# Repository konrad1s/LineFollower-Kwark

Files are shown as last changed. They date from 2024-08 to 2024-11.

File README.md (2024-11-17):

## Introduction

The LineFollower Robot is an autonomous robot designed to follow a predefined path marked by a black or white line.<br>
This project serves a quite advanced solution including hardware project, embedded software and PC QT application.

A short video demo is available on [YouTube](https://www.youtube.com/watch?v=Kh0NfI-lTgY).

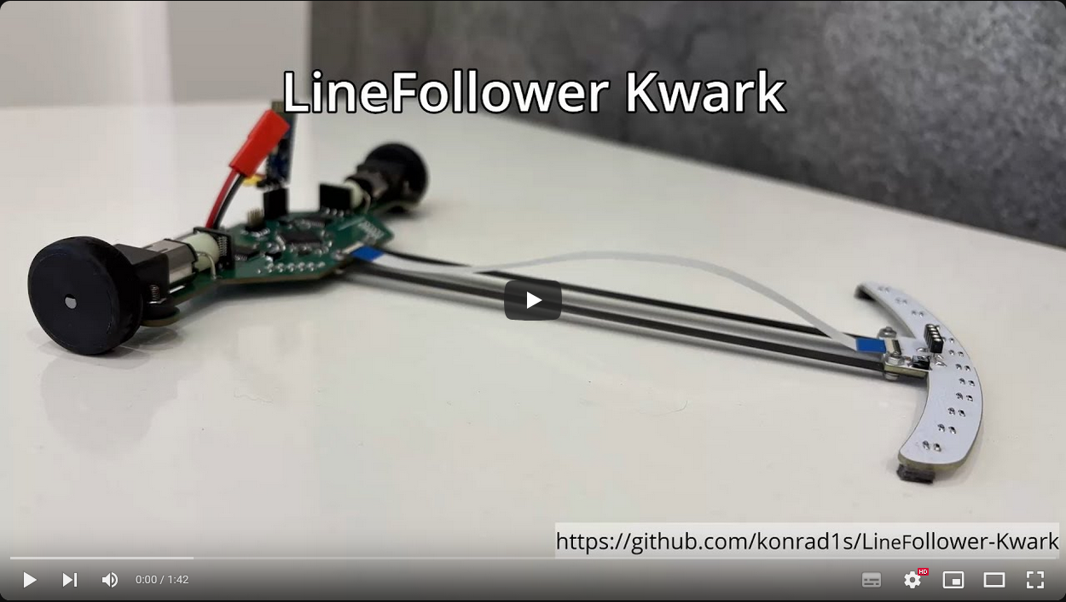
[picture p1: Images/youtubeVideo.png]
LineFollower Youtube Video (https://www.youtube.com/watch?v=Kh0NfI-lTgY)


Example - one of the first - linefollower run:
<p align="center">
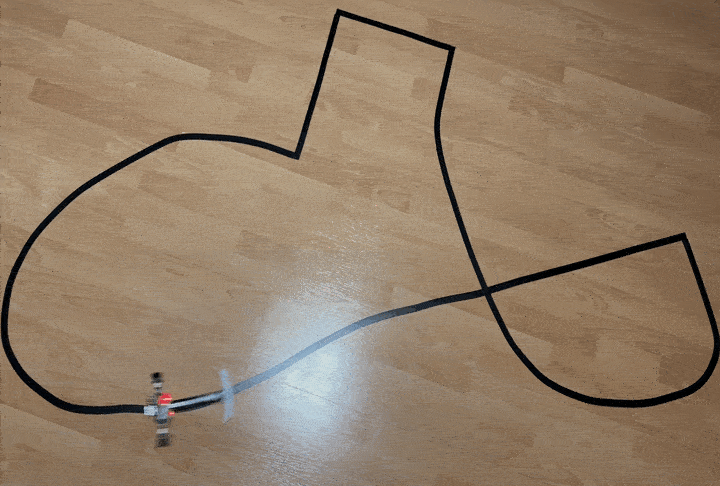
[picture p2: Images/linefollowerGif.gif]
  
</p>

## Hardware
### **High level block diagram**

[![](https://mermaid.ink/img/pako:eNqVlW1vmzAQx7-K5ddJGiCEBE2T8tB2VWHJIM2kOVXlBjdBAxw59tb04bvPxk0ChLYaL8Bnfvf33dkcz3BJIwJduGJ4swaz4SJbZEBeW3Gvp0Y0TUUWLzGPaQZQybzVrLqGiSCc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)](https://mermaid.live/edit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)

### **Schematic and PCB**
Electronic circuit diagrams are available in the [Hardware/release/schematic](Hardware/release/schematic) folder.<br>
Gerbers files are available in the [Hardware/release/gerbers](Hardware/release/gerbers) folder.

**Main board:**
<p align="center">
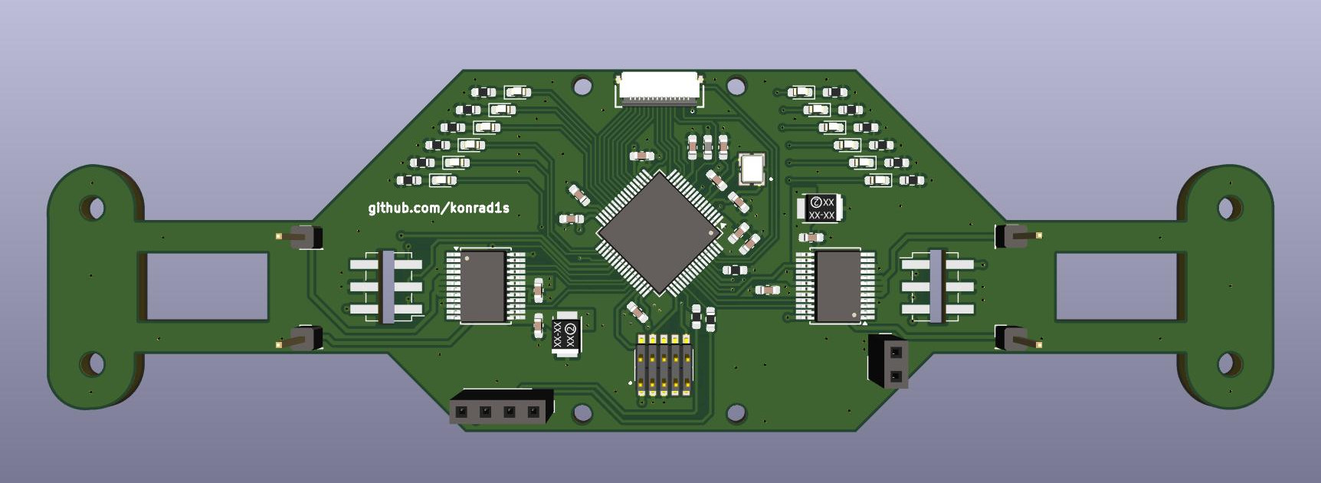
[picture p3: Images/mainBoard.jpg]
  
</p>

**Sensor board:**
<p align="center">
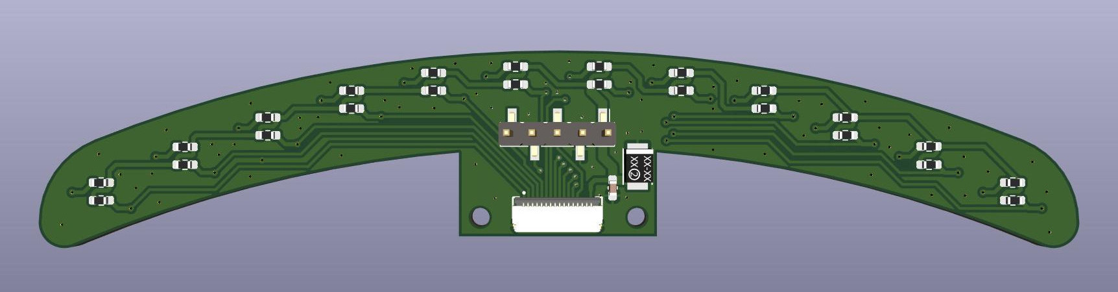
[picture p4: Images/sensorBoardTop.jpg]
  
</p>

**Encoder board:**
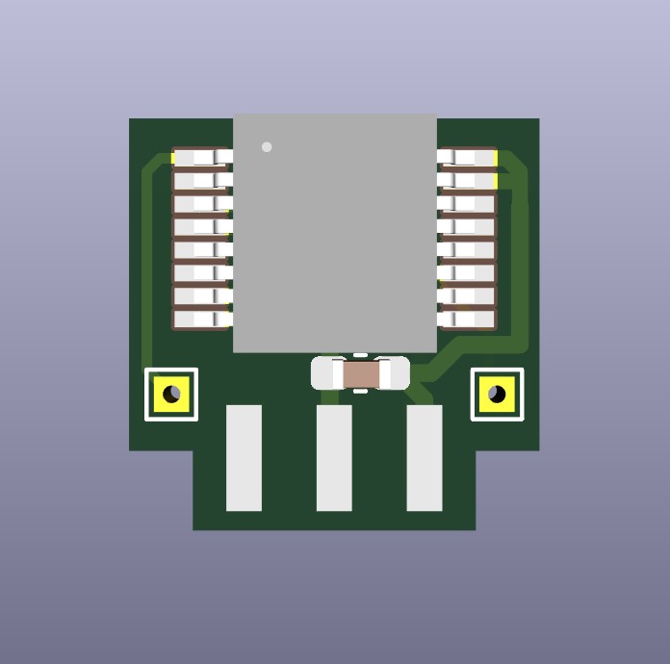
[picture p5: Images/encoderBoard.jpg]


### **Component Details**
1. **STM32F722 MCU** <br>
ARM Cortex M7 microcontroller operating at the 216MHz with FPU, Cache, ITCM, DTCM. It powerful enough to handle algorithms and real-time processing required in linefollower applications.
3. **12x KTIR0711S** <br>
Phototransistor-based infrared sensors used to detect the line by measuring reflected IR light. Arranged in a array at the front of the robot to detect the position of the line. Outputs are connected to the MCU's ADC channels for monitoring.
4. **12x LEDs** <br>
Each LED corresponds to a KTIR0711S sensor, turned on when the sensor detects the line.
5. **2x AMS AS5040 Encoders** <br>
10-bit contactless magnetic rotary encoders providing precise angular position measurements. Thanks to the closed-loop control, encoders enables precise control of motor by providing feedback (velocity) for PID controllers.
6. **2x Pololu TB6612FNG Motor Driver Modules** <br>
H-bridge motor driver modules capable of controlling DC motors. Controller channels are combined to obtain higher current capacity.
7. **2x Pololu Motor 10:1 HPCB 6V DC Motors** <br>
High-power micro metal gearmotors with a 10:1 gear ratio
8. **Bluetooth Module JDY-31** <br>
Bluetooth serial module enables wireless communication between the robot and PC application.
9. **Power Supply Components** <br>
LiPo 7.4V battery used due to high energy density and ability to deliver powerful burst of current.<br>
3.3V Low dropout voltage regulator - steps down the battery voltage for MCU, sensors and others modules.

## Software

### **Main run loop**

The core functionality is implemented through an event-driven state machine. The primary signal is the LF_SIG_ADC_DATA_UPDATED, which is raised whenever new ADC data is available. Currently every 5ms, however increasing this frequency can lead to better control results.

The activity diagram presents simplified main robot algorithm in RUN state:
<p align="center">
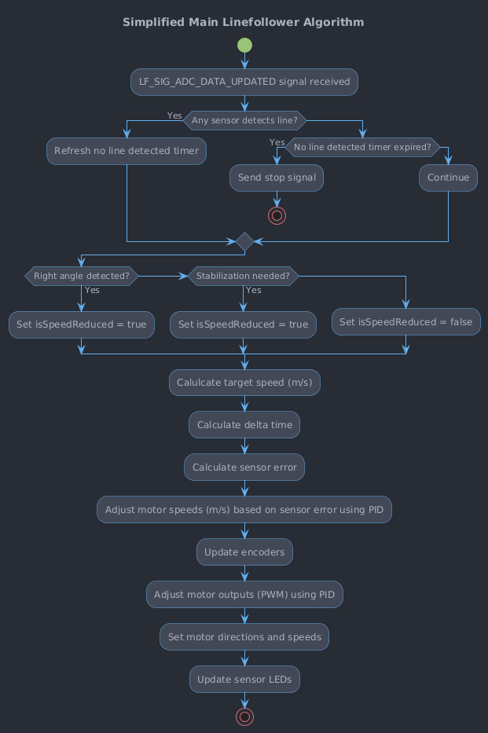
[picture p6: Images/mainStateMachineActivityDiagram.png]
  
</p>

### **Code Structure**

Short brief about implemented software components:

- **linefollower:**
The core component of the software, manages the main event driven state machine. It handles the initialization of all subsystems. This component integrates sensor data processing, PID control algorithms, encoder feedback, and motor management. Additionally, it facilitates communication with the PC application for debugging and configuration purposes.
- **linefollower_config:**
Defines the default configurations and settings for the robot. This ensures that all hardware related configurations is easily adjustable.
- **lf_signal_queue:**
Implements a signal queue used for managing events and signals within the state machine.
- **linefollower_commands:**
Handles the processing of serial communication protocol (SCP) commands received from the PC application. It defines a set of commands for controlling the robot's modes, resetting the MCU, initiating calibration, reading and writing NVM data, toggling debug mode, retrieving session information, and entering the bootloader for firmware updates.
- **lf_calibrate:**
Manages the calibration process for the sensors. It handles the collection of sensor data during calibration runs, computes appropriate threshold values based on the collected values.
- **sensors:**
The module is responsible for interfacing with the robot's sensors to detect the line. It processes ADC data to determine states and manages the associated LEDs. Also implements algorithms to detect specific straight lines and right angles.
- **pid:**
Implements the PID control algorithms used to regulate the robot's motor speeds based on sensor and encoder feedback.
- **encoder:**
Manages the interfacing with the motor encoders to track the robot's velocity.
- **tb6612_motor:**
The module interfaces with the TB6612 motor driver hardware to control the robot's motors.
- **nvm:**
The module handles non-volatile memory operations, enabling the storage and retrieval of configuration data, calibration settings, and runtime parameters. The module ensures data integrity through CRC verification. The nvm module allows the robot to retain configurations across power cycles.
- **scp:**
Implements the Serial Communication Protocol (SCP) used for communication between the robot and external interfaces such as the PC application.
- **scp_dispatcher:**
The module acts as a handler for processing SCP commands received via the scp module. It manages a global command queue using a circular buffer to store incoming data, parses SCP packets, verifies data integrity using CRC, and dispatches valid commands to their respective handlers.

## Bootloader
Implemented bootloader allows for over the air firmware updates without the need of programmer. This is particularly useful for making quick updates "on the road." The bootloader uses the implemented SCP (Serial Communication Protocol) to receive firmware updates over Bluetooth.

There are 2 methods to enter the Bootloader:
1. **Command-Based Entry From Application** <br>
Send a specific command to trigger reset to the bootloader.
2. **Backdoor Entry** <br>
Enter the bootloader upon power-up by sending a specific command. Ensures that firmware updates are always possible, even if the application has errors causing continuous resets.

FLASH memory layout:
<p align="center">
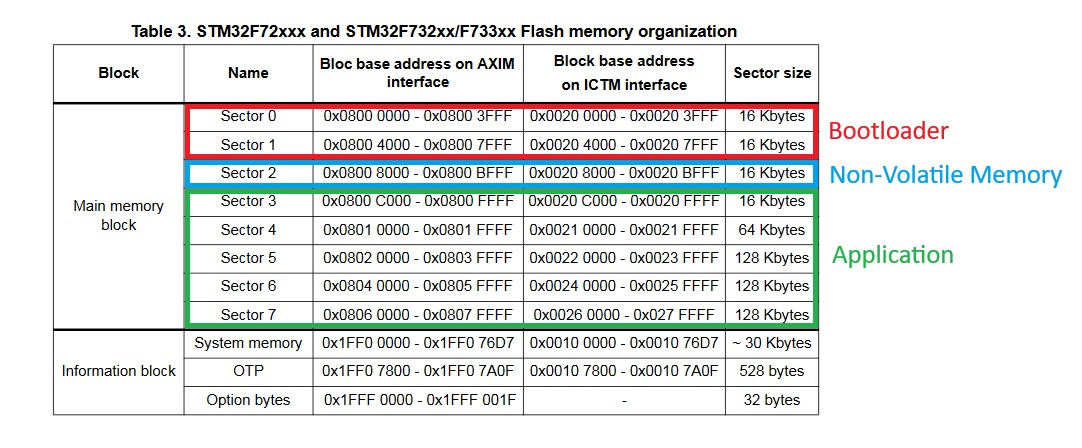
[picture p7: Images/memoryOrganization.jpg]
  
</p>

## **QT Application**

The QT Application provides a graphical interface to control, configure, and monitor the robot. The main sections of the interface and their functionalities are as follows:
1. **Connection Panel** <br>
Connection indicator and buttons to establish or terminate Bluetooth communication.
2. **Control Panel**<br>
Starting, stopping, resetting, and calibrating the robot, along with options to enable debug mode, read/write NVM, and display real-time data (speed, error, and timing metrics).
3. **Sensors Panel**<br>
Real-time sensor data display showing actual values, calibration references, and sensor weights.
4. **Configuration**<br>
Includes settings for general parameters, PID tuning for motor control, and encoder adjustments.
5. **Graph**<br>
A real-time graph displaying motor speeds, speed reduction, sensors error, enabling data analysis and adjustments for optimal performance.
6. **Bootloader**<br>
Firmware update controls, including options to enter bootloader mode, switch to the main application and flash new firmware via Bluetooth.
7. **Logs**<br>
Real-time log display with options to save or clear logs, providing detailed event tracking for debugging.

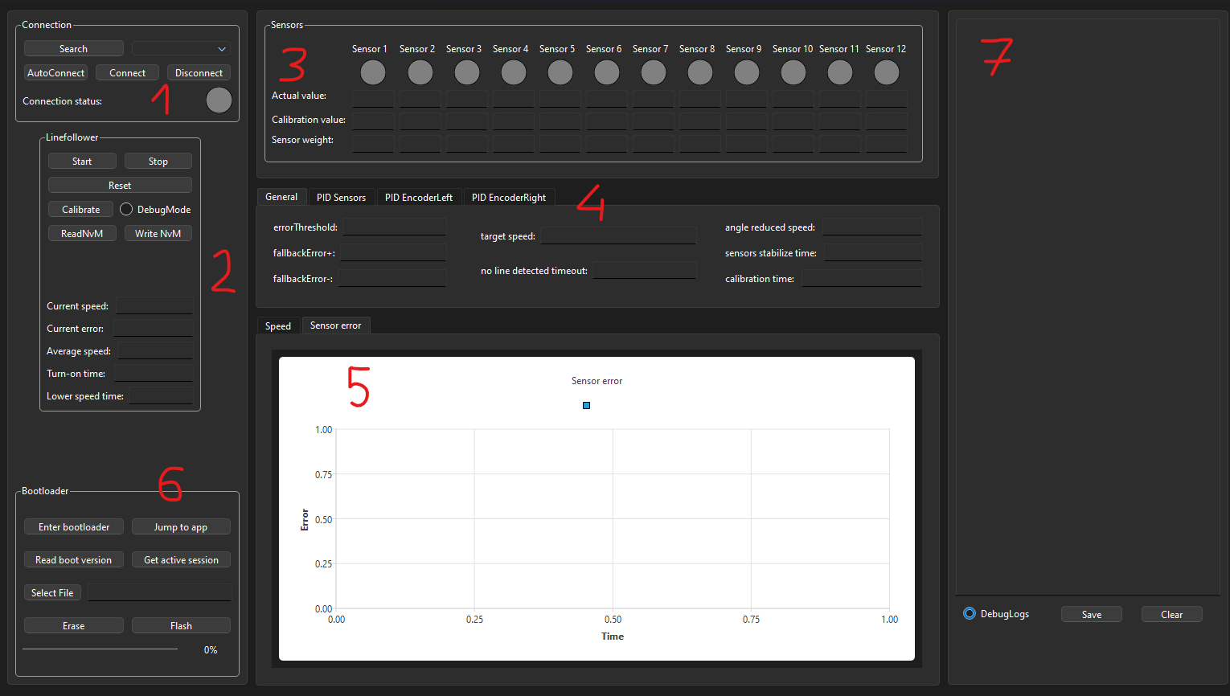
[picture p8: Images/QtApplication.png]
QtApplication


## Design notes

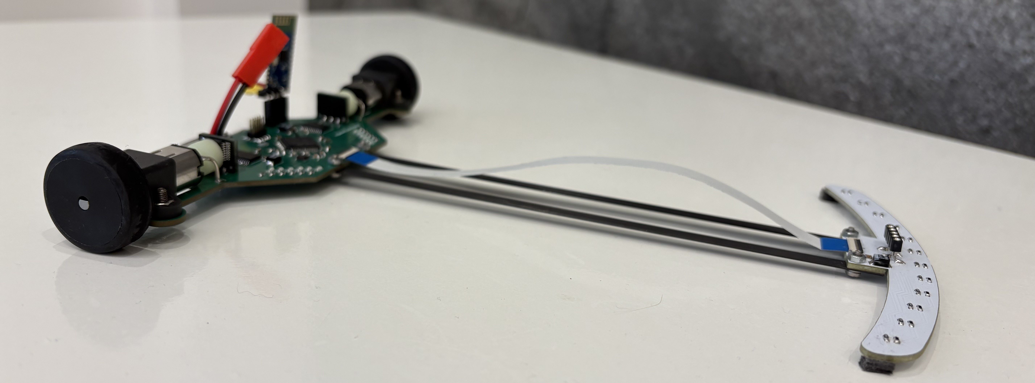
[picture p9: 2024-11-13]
Images/linefollower.jpg

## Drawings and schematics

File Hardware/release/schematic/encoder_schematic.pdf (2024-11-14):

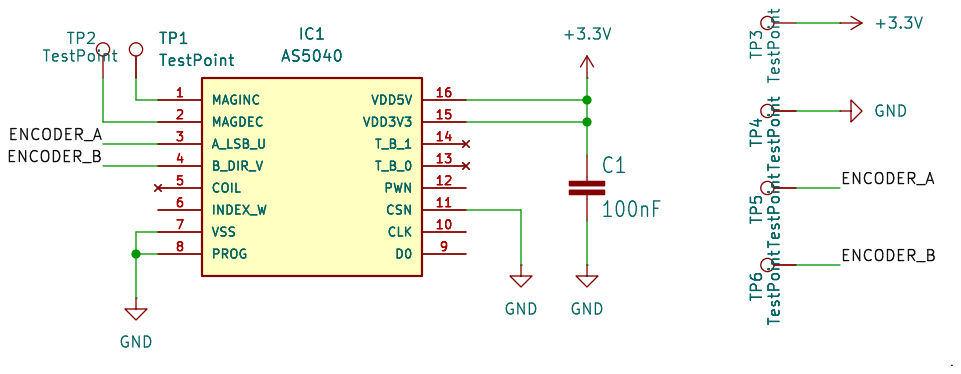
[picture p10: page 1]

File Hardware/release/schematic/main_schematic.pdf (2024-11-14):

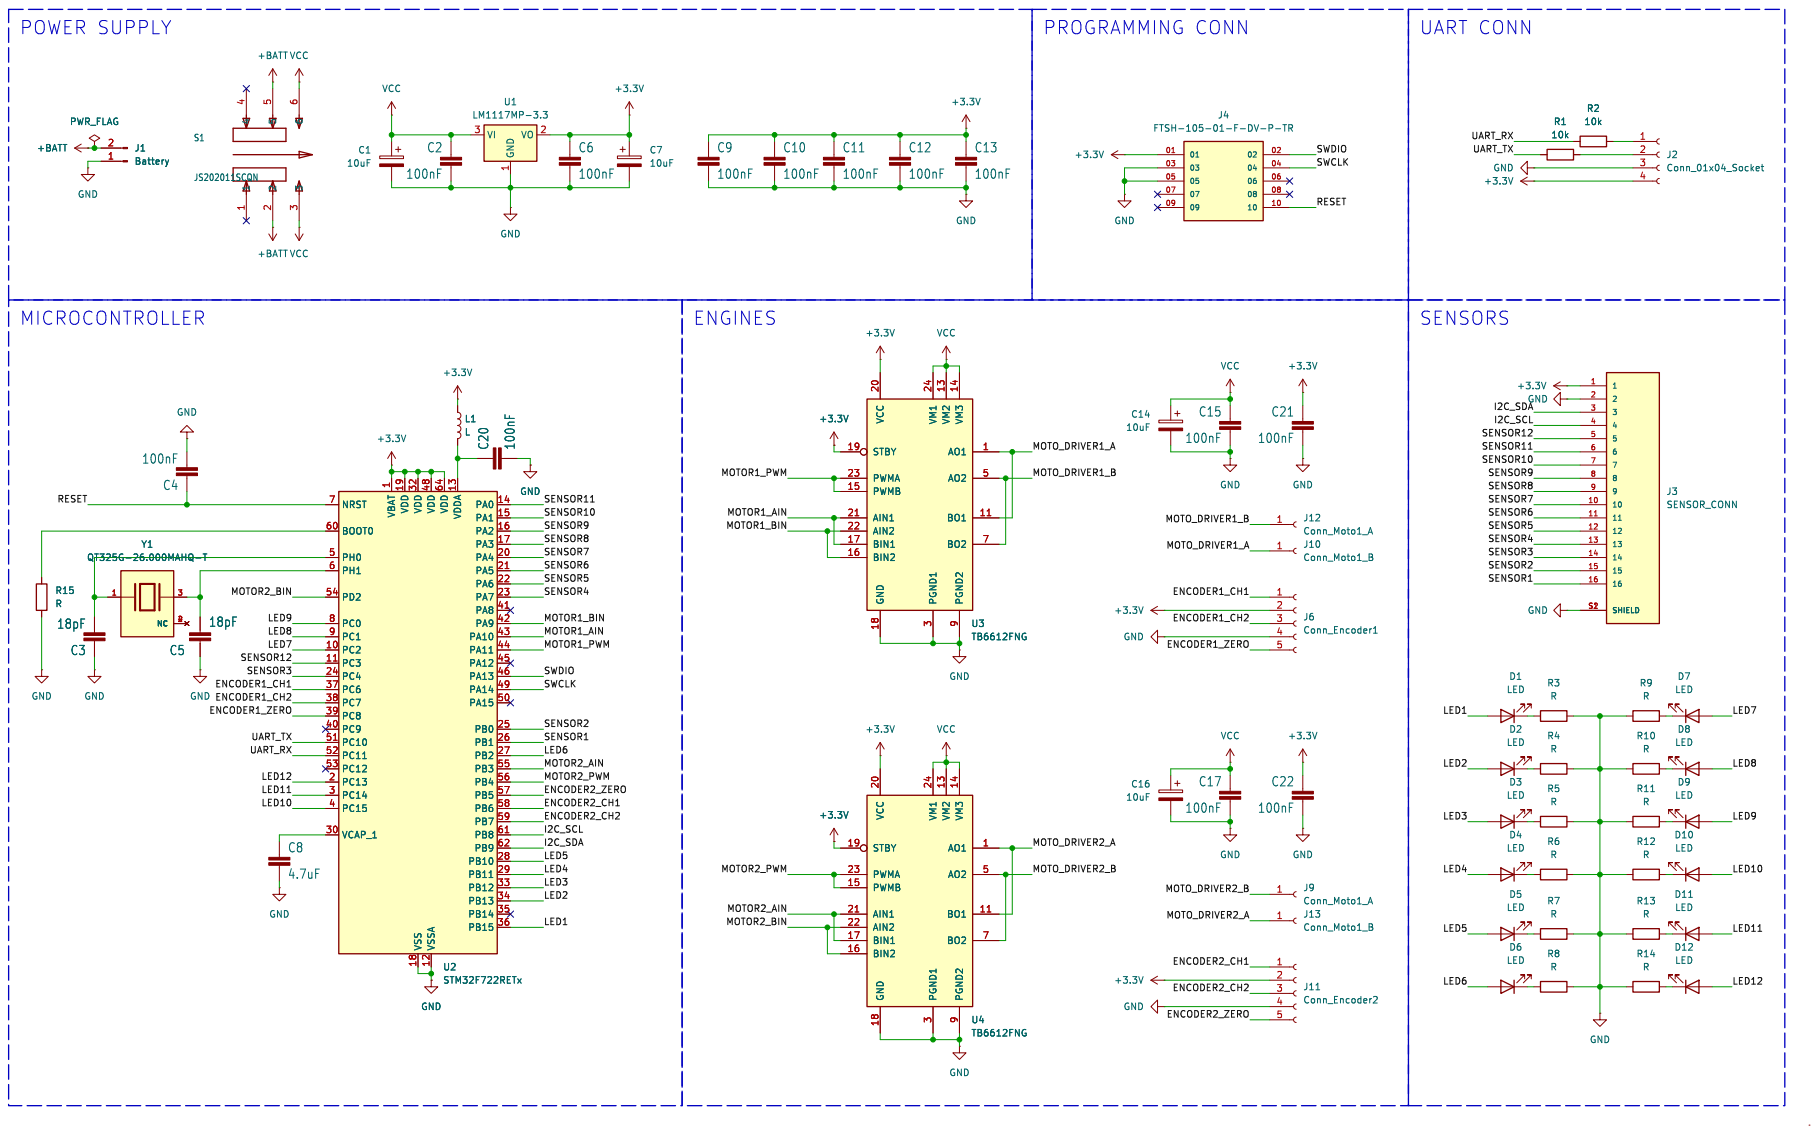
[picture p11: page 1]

1 PC2 10 PC3 11 VSSA 12 VDDA 13 PA0 14 PA1 15 PA2 16 PA3 17 VSS 18 VDD 19 PC13 2 PA4 20 PA5 21 PA6 22 PA7 23 PC4 24 PB0 25 PB1 26 PB2 27 PB10 28 PB11 29 PC14 3 VCAP_1 30 VDD 32 PB12 33 PB13 34 PB14 35 PB15 36 PC6 37 PC7 38 PC8 39 PC15 4 PC9 40 PA8 41 PA9 42 PA10 43 PA11 44 PA12 45 PA13 46 VDD 48 PA14 49 PH0 5 PA15 50 PC10 51 PC11 52 PC12 53 PD2 54 PB3 55 PB4 56 PB5 57 PB6 58 PB7 59 PH1 6 BOOT0 60 PB8 61 PB9 62 VDD 64 NRST 7 PC0 8 PC1 9 GND C3

1 PC2 10 PC3 11 VSSA 12 VDDA 13 PA0 14 PA1 15 PA2 16 PA3 17 VSS 18 VDD 19 PC13 2 PA4 20 PA5 21 PA6 22 PA7 23 PC4 24 PB0 25 PB1 26 PB2 27 PB10 28 PB11 29 PC14 3 VCAP_1 30 VDD 32 PB12 33 PB13 34 PB14 35 PB15 36 PC6 37 PC7 38 PC8 39 PC15 4 PC9 40 PA8 41 PA9 42 PA10 43 PA11 44 PA12 45 PA13 46 VDD 48 PA14 49 PH0 5 PA15 50 PC10 51 PC11 52 PC12 53 PD2 54 PB3 55 PB4 56 PB5 57 PB6 58 PB7 59 PH1 6 BOOT0 60 PB8 61 PB9 62 VDD 64 NRST 7 PC0 8 PC1 9 U2STM32F722RETx C8

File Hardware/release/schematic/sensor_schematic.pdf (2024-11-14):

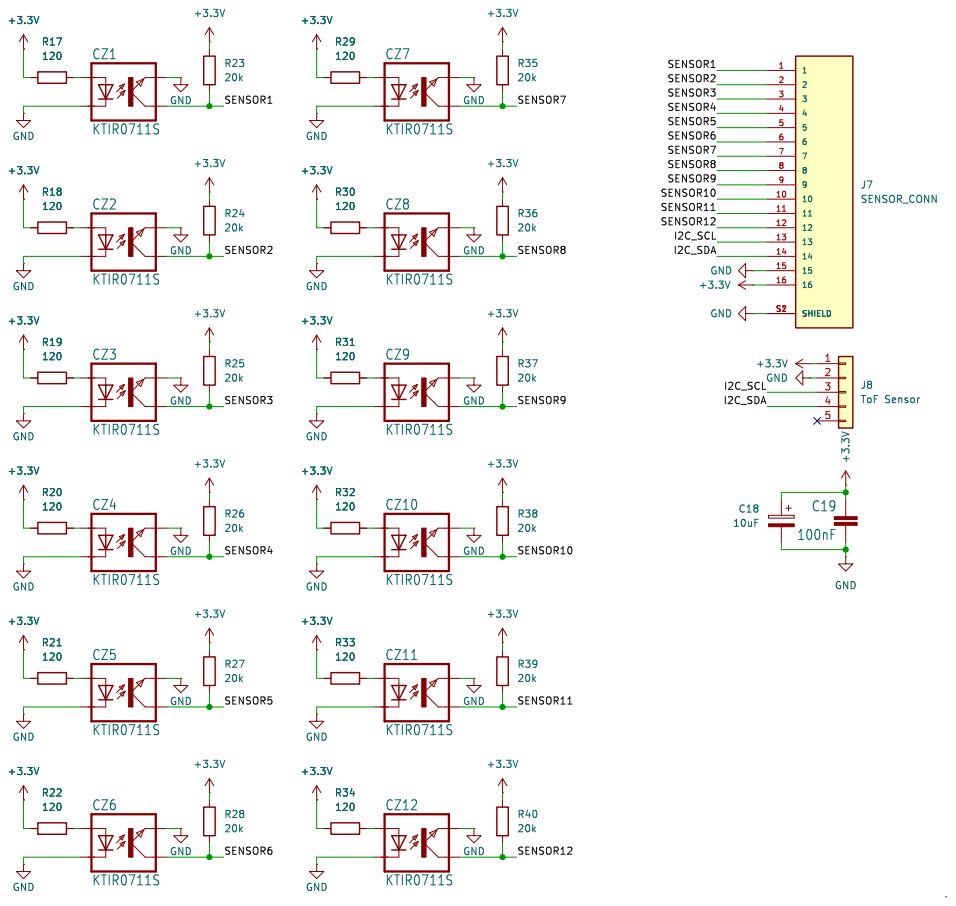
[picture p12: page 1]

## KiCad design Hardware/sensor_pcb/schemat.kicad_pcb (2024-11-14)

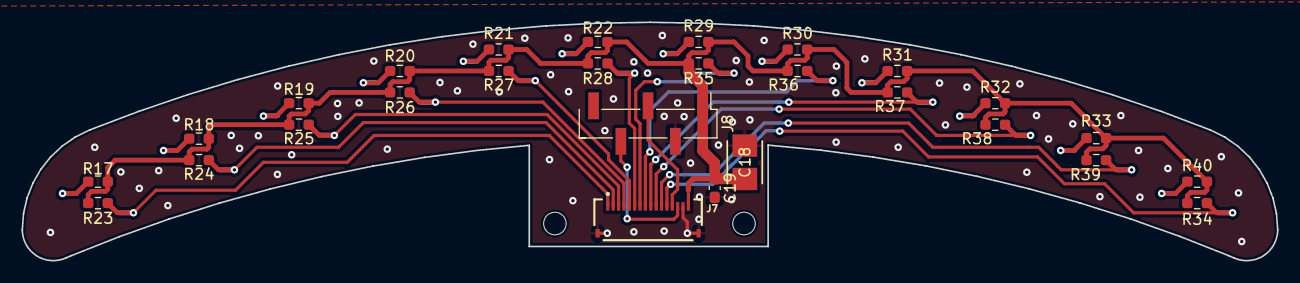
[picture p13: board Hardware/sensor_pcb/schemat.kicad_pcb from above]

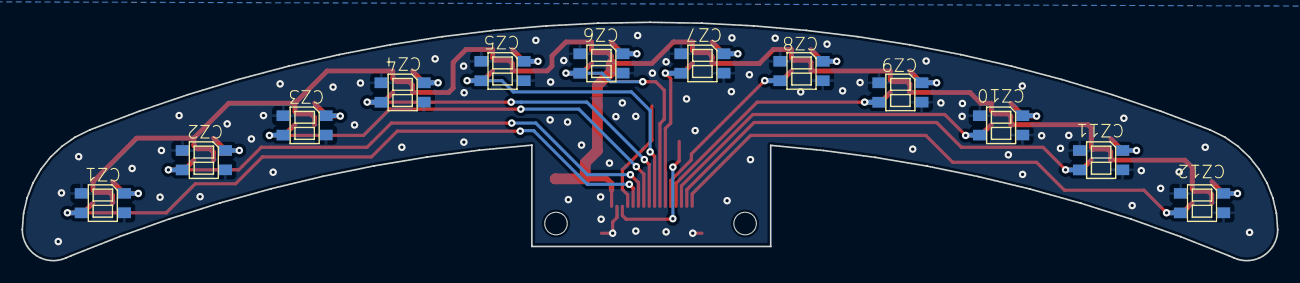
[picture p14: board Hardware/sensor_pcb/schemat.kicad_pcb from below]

Board: 2 copper layers, 116.8 x 22.2 mm, 42 parts (12 on the bottom side), 28 nets.

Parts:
@HOLE8, @HOLE9: (no value)
C18: 10uF; CAP_293D-B_VSS
C19: 100nF; C_0603_1608Metric_Pad1.08x0.95mm_HandSolder
CZ1, CZ2, CZ3, CZ4, CZ5, CZ6, CZ7, CZ8, CZ9, CZ10, CZ11, CZ12: KTIR0711S; TOP
J7: SENSOR_CONN; GCT_FFC2B28-16-G
J8: ToF Sensor; PinHeader_1x05_P2.54mm_Vertical_SMD_Pin1Left
R17, R18, R19, R20, R21, R22, R29, R30, R31, R32, R33, R34: 120; R_0603_1608Metric_Pad0.98x0.95mm_HandSolder
R23, R24, R25, R26, R27, R28, R35, R36, R37, R38, R39, R40: 20k; R_0603_1608Metric_Pad0.98x0.95mm_HandSolder

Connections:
+3.3V: C18.1, C19.1, J7.16, J8.1, R17.1, R18.1, R19.1, R20.1, R21.1, R22.1, R23.1, R24.1, R25.1, R26.1, R27.1, R28.1, R29.1, R30.1, R31.1, R32.1, R33.1, R34.1, R35.1, R36.1, R37.1, R38.1, R39.1, R40.1
/schemat_2/I2C_SCL: J7.13, J8.3
/schemat_2/I2C_SDA: J7.14, J8.4
/schemat_2/SENSOR1: CZ12.KOLEKTOR, J7.1, R23.2
/schemat_2/SENSOR2: CZ11.KOLEKTOR, J7.2, R24.2
/schemat_2/SENSOR3: CZ10.KOLEKTOR, J7.3, R25.2
/schemat_2/SENSOR4: CZ9.KOLEKTOR, J7.4, R26.2
/schemat_2/SENSOR5: CZ8.KOLEKTOR, J7.5, R27.2
/schemat_2/SENSOR6: CZ7.KOLEKTOR, J7.6, R28.2
/schemat_2/SENSOR7: CZ6.KOLEKTOR, J7.7, R35.2
/schemat_2/SENSOR8: CZ5.KOLEKTOR, J7.8, R36.2
/schemat_2/SENSOR9: CZ4.KOLEKTOR, J7.9, R37.2
/schemat_2/SENSOR10: CZ3.KOLEKTOR, J7.10, R38.2
/schemat_2/SENSOR11: CZ2.KOLEKTOR, J7.11, R39.2
/schemat_2/SENSOR12: CZ1.KOLEKTOR, J7.12, R40.2
GND: C18.2, C19.2, CZ1.EMITER, CZ1.KATODA, CZ2.EMITER, CZ2.KATODA, CZ3.EMITER, CZ3.KATODA, CZ4.EMITER, CZ4.KATODA, CZ5.EMITER, CZ5.KATODA, CZ6.EMITER, CZ6.KATODA, CZ7.EMITER, CZ7.KATODA, CZ8.EMITER, CZ8.KATODA, CZ9.EMITER, CZ9.KATODA, CZ10.EMITER, CZ10.KATODA, CZ11.EMITER, CZ11.KATODA, CZ12.EMITER, CZ12.KATODA, J7.15, J7.S1 (SHIELD), J7.S2 (SHIELD), J8.2
unnamed: CZ1.ANODA, R34.2
unnamed: CZ2.ANODA, R33.2
unnamed: CZ3.ANODA, R32.2
unnamed: CZ4.ANODA, R31.2
unnamed: CZ5.ANODA, R30.2
unnamed: CZ6.ANODA, R29.2
unnamed: CZ7.ANODA, R22.2
unnamed: CZ8.ANODA, R21.2
unnamed: CZ9.ANODA, R20.2
unnamed: CZ10.ANODA, R19.2
unnamed: CZ11.ANODA, R18.2
unnamed: CZ12.ANODA, R17.2

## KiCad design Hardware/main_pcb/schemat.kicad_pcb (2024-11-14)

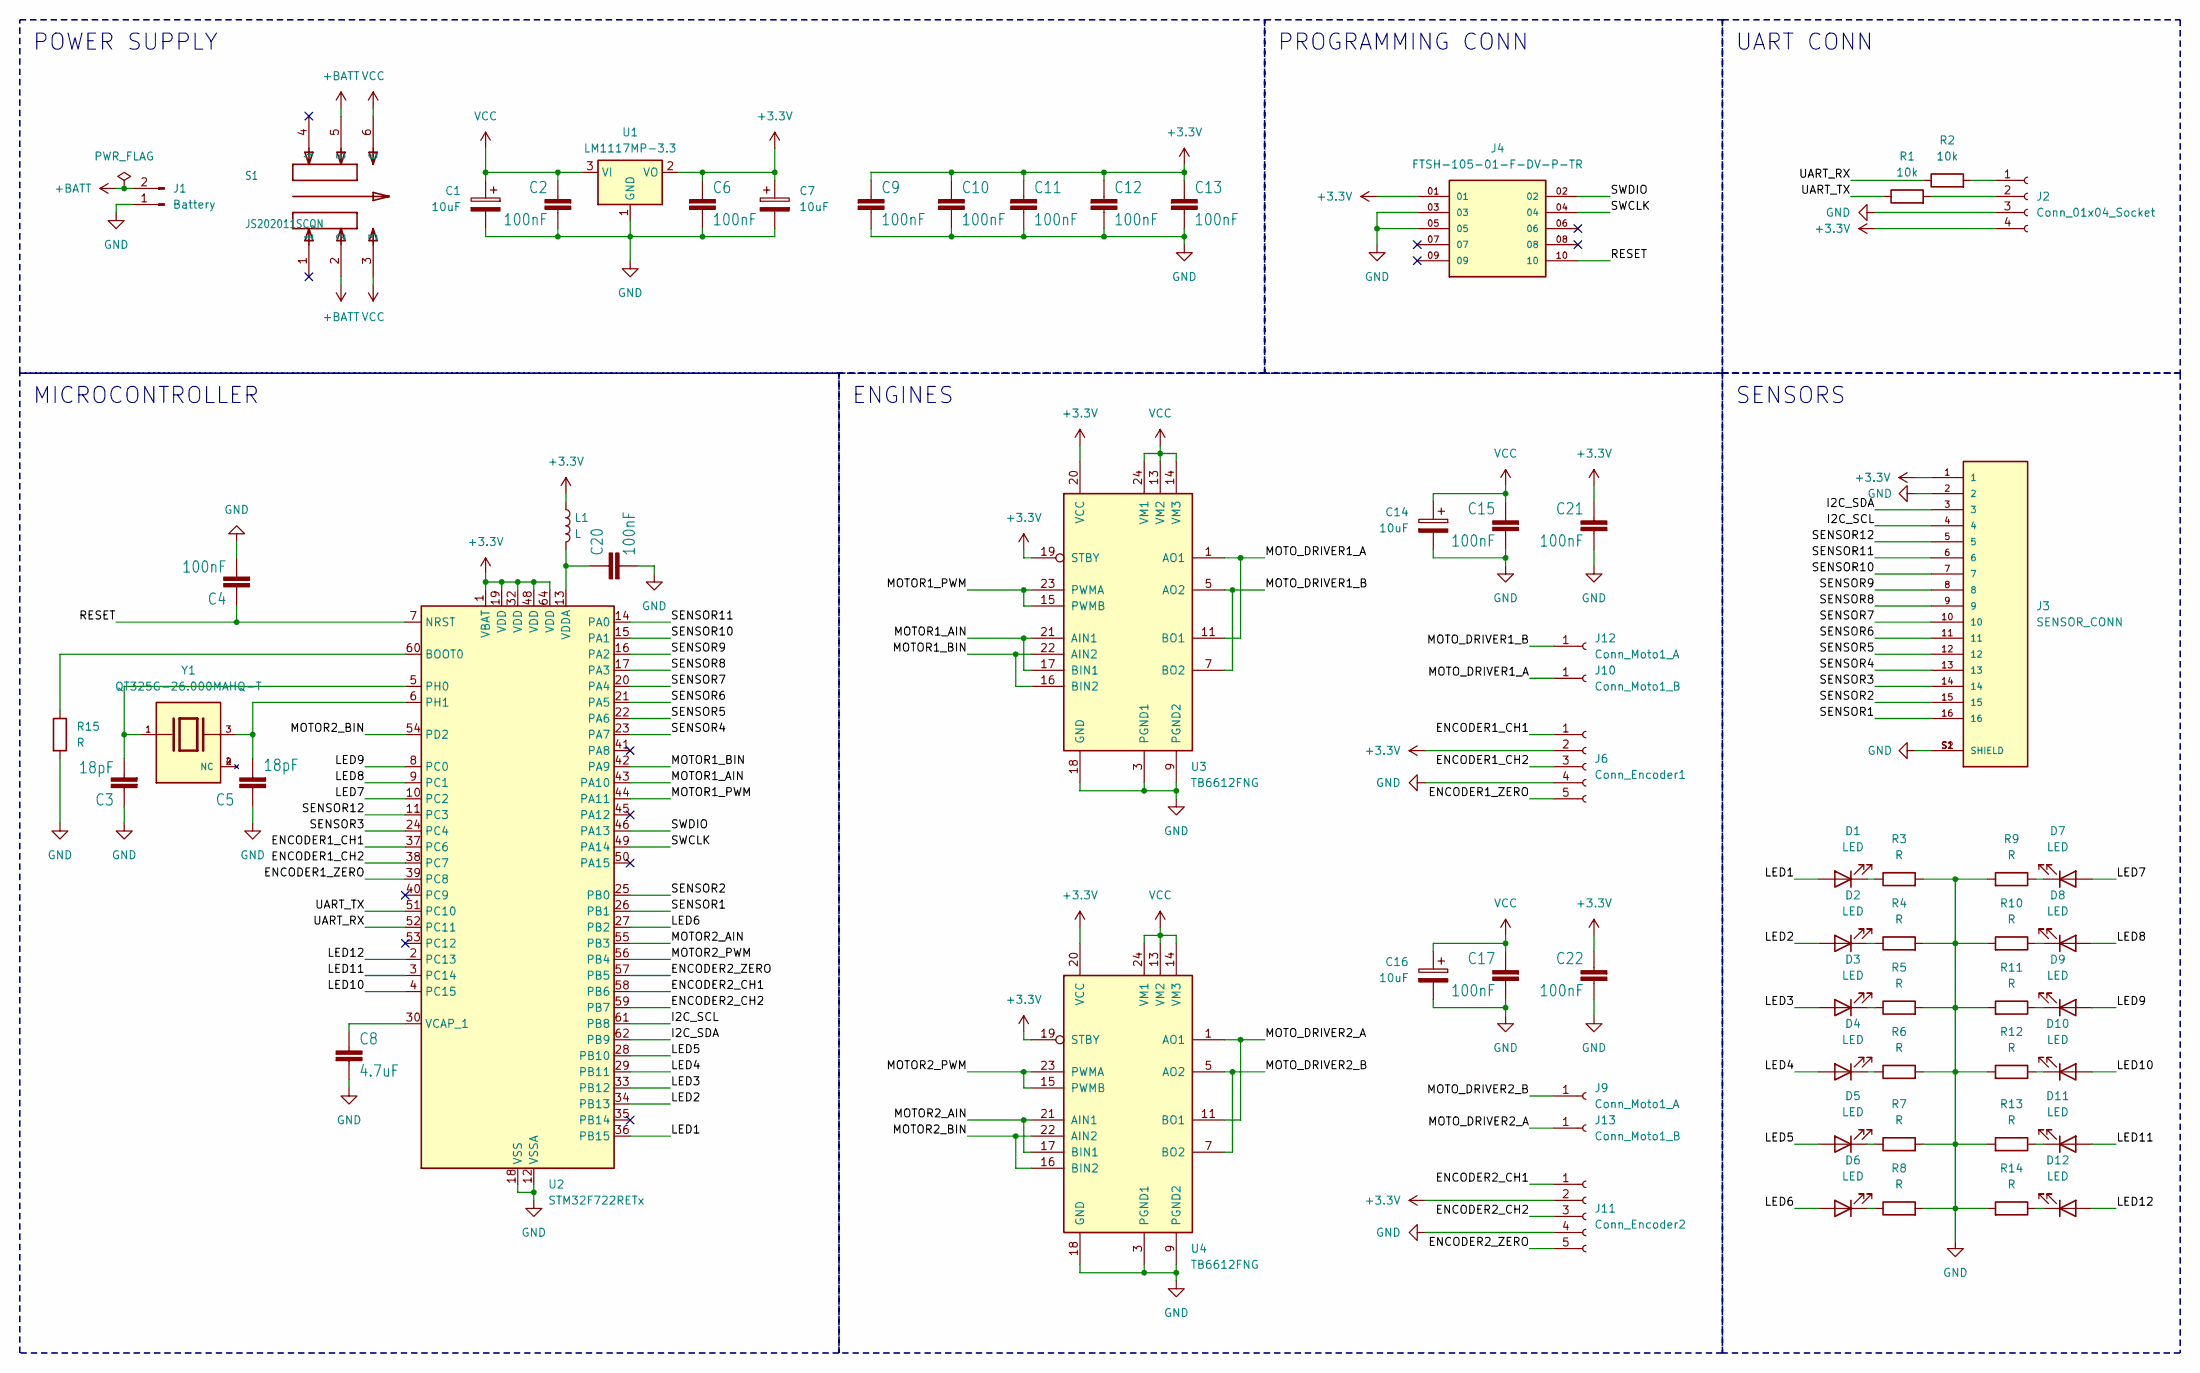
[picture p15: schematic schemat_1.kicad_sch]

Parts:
C1, C7, C14, C16: 10uF; CAP_293D-B_VSS
C2, C4, C6, C9, C10, C11, C12, C13, C15, C17, C20, C21, C22: 100nF; C_0603_1608Metric_Pad1.08x0.95mm_HandSolder
C3, C5: 18pF; C_0603_1608Metric_Pad1.08x0.95mm_HandSolder
C8: 4.7uF; C_0603_1608Metric_Pad1.08x0.95mm_HandSolder
D1, D2, D3, D4, D5, D6, D7, D8, D9, D10, D11, D12: LED; LED_0603_1608Metric_Pad1.05x0.95mm_HandSolder
J1: Battery; PinSocket_1x02_P2.54mm_Vertical
J2: Conn_01x04_Socket; PinSocket_1x04_P2.54mm_Vertical
J3: SENSOR_CONN; GCT_FFC2B28-16-G; PARTREV A
J4: FTSH-105-01-F-DV-P-TR; SAMTEC_FTSH-105-01-F-DV-P-TR; PARTREV R
J6: Conn_Encoder1; PinHeader_2x03_P2.54mm_Vertical_SMD
J9, J12: Conn_Moto1_A; PinHeader_1x01_P2.54mm_Vertical
J10, J13: Conn_Moto1_B; PinHeader_1x01_P2.54mm_Vertical
J11: Conn_Encoder2; PinHeader_2x03_P2.54mm_Vertical_SMD
L1: L; L_0603_1608Metric_Pad1.05x0.95mm_HandSolder
R1, R2: 10k; R_0603_1608Metric_Pad0.98x0.95mm_HandSolder
R3, R4, R5, R6, R7, R8, R9, R10, R11, R12, R13, R14, R15: R; R_0603_1608Metric_Pad0.98x0.95mm_HandSolder
S1: JS202011SCQN; SW_JS202011SCQN
U1: LM1117MP-3.3; SOT-223-3_TabPin2
U2: STM32F722RETx; LQFP-64_10x10mm_P0.5mm
U3, U4: TB6612FNG; SSOP-24_5.3x8.2mm_P0.65mm
Y1: QT325G-26.000MAHQ-T; XTAL_QT325G-26.000MAHQ-T; PARTREV N/A

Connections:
+3.3V: C6.1, C7.1, C9.1, C10.1, C11.1, C12.1, C13.1, C21.1, C22.1, J2.4, J3.1, J4.01, J6.2, J11.2, L1.1, U1.2 (VO), U2.1 (VBAT), U2.19 (VDD), U2.32 (VDD), U2.48 (VDD), U2.64 (VDD), U3.19 (STBY), U3.20 (VCC), U4.19 (STBY), U4.20 (VCC)
+BATT: J1.2, S1.2, S1.5
/schemat_1/ENCODER1_CH1: J6.1, U2.37 (PC6)
/schemat_1/ENCODER1_CH2: J6.3, U2.38 (PC7)
/schemat_1/ENCODER1_ZERO: J6.5, U2.39 (PC8)
/schemat_1/ENCODER2_CH1: J11.1, U2.58 (PB6)
/schemat_1/ENCODER2_CH2: J11.3, U2.59 (PB7)
/schemat_1/ENCODER2_ZERO: J11.5, U2.57 (PB5)
/schemat_1/I2C_SCL: J3.4, U2.61 (PB8)
/schemat_1/I2C_SDA: J3.3, U2.62 (PB9)
/schemat_1/LED1: D1.2 (A), U2.36 (PB15)
/schemat_1/LED2: D2.2 (A), U2.34 (PB13)
/schemat_1/LED3: D3.2 (A), U2.33 (PB12)
/schemat_1/LED4: D4.2 (A), U2.29 (PB11)
/schemat_1/LED5: D5.2 (A), U2.28 (PB10)
/schemat_1/LED6: D6.2 (A), U2.27 (PB2)
/schemat_1/LED7: D7.2 (A), U2.10 (PC2)
/schemat_1/LED8: D8.2 (A), U2.9 (PC1)
/schemat_1/LED9: D9.2 (A), U2.8 (PC0)
/schemat_1/LED10: D10.2 (A), U2.4 (PC15)
/schemat_1/LED11: D11.2 (A), U2.3 (PC14)
/schemat_1/LED12: D12.2 (A), U2.2 (PC13)
/schemat_1/MOTOR1_AIN: U2.43 (PA10), U3.17 (BIN1), U3.21 (AIN1)
/schemat_1/MOTOR1_BIN: U2.42 (PA9), U3.16 (BIN2), U3.22 (AIN2)
/schemat_1/MOTOR1_PWM: U2.44 (PA11), U3.15 (PWMB), U3.23 (PWMA)
/schemat_1/MOTOR2_AIN: U2.55 (PB3), U4.17 (BIN1), U4.21 (AIN1)
/schemat_1/MOTOR2_BIN: U2.54 (PD2), U4.16 (BIN2), U4.22 (AIN2)
/schemat_1/MOTOR2_PWM: U2.56 (PB4), U4.15 (PWMB), U4.23 (PWMA)
/schemat_1/MOTO_DRIVER1_A: J10.1, U3.1 (AO1), U3.2 (AO1), U3.11 (BO1), U3.12 (BO1)
/schemat_1/MOTO_DRIVER1_B: J12.1, U3.5 (AO2), U3.6 (AO2), U3.7 (BO2), U3.8 (BO2)
/schemat_1/MOTO_DRIVER2_A: J13.1, U4.1 (AO1), U4.2 (AO1), U4.11 (BO1), U4.12 (BO1)
/schemat_1/MOTO_DRIVER2_B: J9.1, U4.5 (AO2), U4.6 (AO2), U4.7 (BO2), U4.8 (BO2)
/schemat_1/RESET: C4.1, J4.10, U2.7 (NRST)
/schemat_1/SENSOR1: J3.16, U2.26 (PB1)
/schemat_1/SENSOR2: J3.15, U2.25 (PB0)
/schemat_1/SENSOR3: J3.14, U2.24 (PC4)
/schemat_1/SENSOR4: J3.13, U2.23 (PA7)
/schemat_1/SENSOR5: J3.12, U2.22 (PA6)
/schemat_1/SENSOR6: J3.11, U2.21 (PA5)
/schemat_1/SENSOR7: J3.10, U2.20 (PA4)
/schemat_1/SENSOR8: J3.9, U2.17 (PA3)
/schemat_1/SENSOR9: J3.8, U2.16 (PA2)
/schemat_1/SENSOR10: J3.7, U2.15 (PA1)
/schemat_1/SENSOR11: J3.6, U2.14 (PA0)
/schemat_1/SENSOR12: J3.5, U2.11 (PC3)
/schemat_1/SWCLK: J4.04, U2.49 (PA14)
/schemat_1/SWDIO: J4.02, U2.46 (PA13)
/schemat_1/UART_RX: R2.1, U2.52 (PC11)
/schemat_1/UART_TX: R1.1, U2.51 (PC10)
GND: C1.2, C2.2, C3.1, C4.2, C5.1, C6.2, C7.2, C8.2, C9.2, C10.2, C11.2, C12.2, C13.2, C14.2, C15.2, C16.2, C17.2, C20.2, C21.2, C22.2, J1.1, J2.3, J3.2, J3.S1 (SHIELD), J3.S2 (SHIELD), J4.03, J4.05, J6.4, J11.4, R3.2, R4.2, R5.2, R6.2, R7.2, R8.2, R9.2, R10.2, R11.2, R12.2, R13.2, R14.2, R15.2, U1.1 (GND), U2.12 (VSSA), U2.18 (VSS), U2.31 (VSS), U2.47 (VSS), U2.63 (VSS), U3.3 (PGND1), U3.4 (PGND1), U3.9 (PGND2), U3.10 (PGND2), U3.18 (GND), U4.3 (PGND1), U4.4 (PGND1), U4.9 (PGND2), U4.10 (PGND2), U4.18 (GND)
unnamed: D1.1 (K), R3.1
unnamed: D2.1 (K), R4.1
unnamed: D3.1 (K), R5.1
unnamed: D4.1 (K), R6.1
unnamed: D5.1 (K), R7.1
unnamed: D6.1 (K), R8.1
unnamed: D7.1 (K), R9.1
unnamed: D8.1 (K), R10.1
unnamed: D9.1 (K), R11.1
unnamed: D10.1 (K), R12.1
unnamed: D11.1 (K), R13.1
unnamed: D12.1 (K), R14.1
unnamed: J2.1, R2.2
unnamed: J2.2, R1.2
unnamed: R15.1, U2.60 (BOOT0)
unnamed: C3.2, U2.5 (PH0), Y1.1
unnamed: C5.2, U2.6 (PH1), Y1.3
unnamed: C8.1, U2.30 (VCAP_1)
unnamed: C20.1, L1.2, U2.13 (VDDA)
VCC: C1.1, C2.1, C14.1, C15.1, C16.1, C17.1, S1.3, S1.6, U1.3 (VI), U3.13 (VM2), U3.14 (VM3), U3.24 (VM1), U4.13 (VM2), U4.14 (VM3), U4.24 (VM1)

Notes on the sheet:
UART CONN
ENGINES
PROGRAMMING CONN
POWER SUPPLY
SENSORS
MICROCONTROLLER

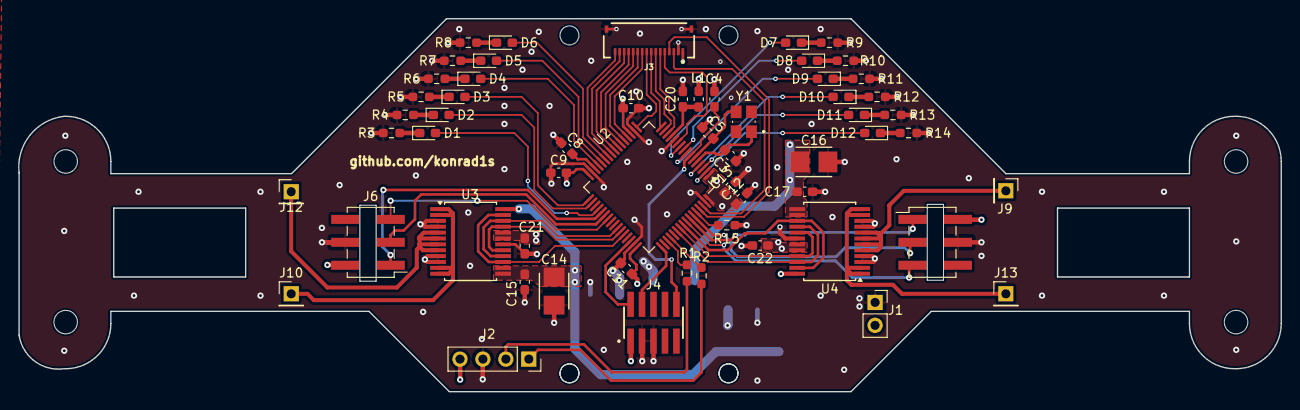
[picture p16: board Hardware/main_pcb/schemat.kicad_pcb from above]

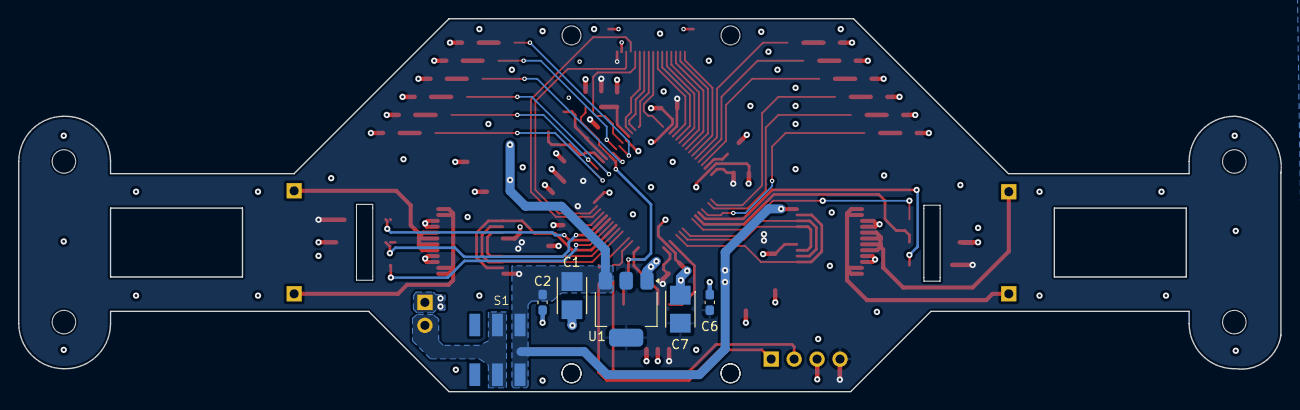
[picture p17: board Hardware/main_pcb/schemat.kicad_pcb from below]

Board: 4 copper layers, 139.7 x 41.3 mm, 72 parts (6 on the bottom side), 70 nets.

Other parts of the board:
@HOLE0, @HOLE1, @HOLE2, @HOLE3, @HOLE8, @HOLE8#2, @HOLE9, @HOLE9#2: (no value)

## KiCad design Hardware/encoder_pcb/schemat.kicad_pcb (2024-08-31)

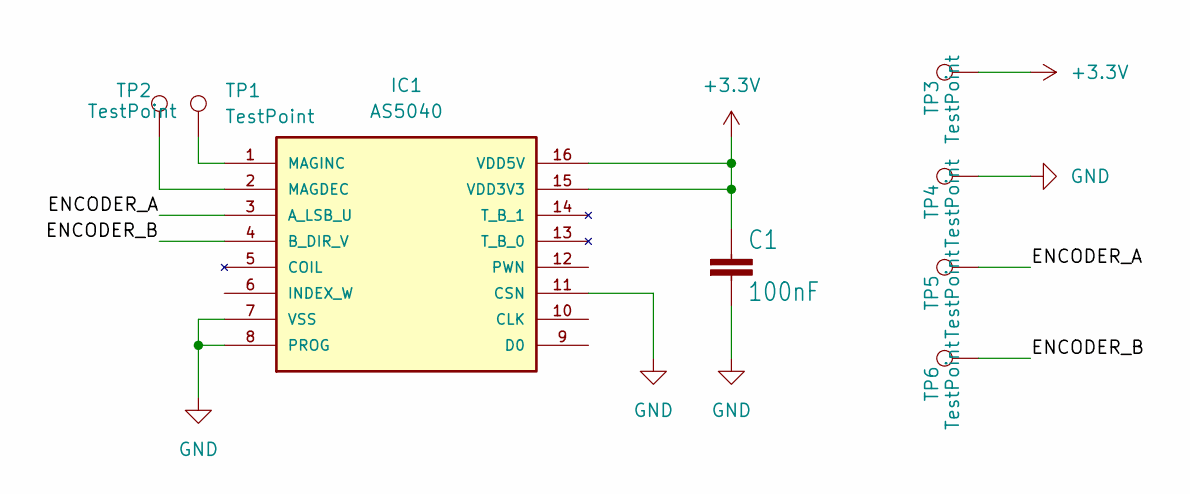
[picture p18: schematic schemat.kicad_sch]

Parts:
C1: 100nF; C_0603_1608Metric_Pad1.08x0.95mm_HandSolder
IC1: AS5040; SSOP16
TP1, TP2: TestPoint; TestPoint_THTPad_1.0x1.0mm_Drill0.5mm
TP3, TP4, TP5, TP6: TestPoint; SolderWirePad_1x01_SMD_1x2mm

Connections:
+3.3V: C1.1, IC1.15 (VDD3V3), IC1.16 (VDD5V), TP3.1
/ENCODER_A: IC1.3 (A_LSB_U), TP5.1
/ENCODER_B: IC1.4 (B_DIR_V), TP6.1
GND: C1.2, IC1.7 (VSS), IC1.8 (PROG), IC1.11 (CSN), TP4.1
unnamed: IC1.2 (MAGDEC), TP2.1
unnamed: IC1.1 (MAGINC), TP1.1

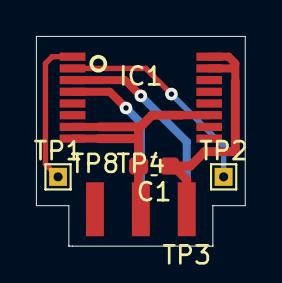
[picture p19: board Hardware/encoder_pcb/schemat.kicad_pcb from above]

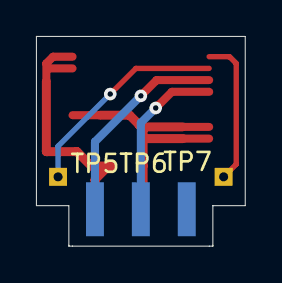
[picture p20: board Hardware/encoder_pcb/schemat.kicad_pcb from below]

Board: 2 copper layers, 11.6 x 11.6 mm, 10 parts (3 on the bottom side), 6 nets.

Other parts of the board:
TP7, TP8: TestPoint; SolderWirePad_1x01_SMD_1x2mm

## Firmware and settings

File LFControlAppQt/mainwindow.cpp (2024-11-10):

#include "mainwindow.h"
#include "./ui_mainwindow.h"
#include "debugdata.h"
#include <QDateTime.h>
#include <QFileDialog>
#include <QFile>
#include <QTextStream>
#include <QMessageBox>


MainWindow::MainWindow(QWidget *parent)
    : QMainWindow(parent), ui(new Ui::MainWindow),
    bluetoothHandler(new BluetoothHandler(this)),
    bootloader(new Bootloader(bluetoothHandler, this)),
    autoConnectInProgress(false),
    wasSpeedReduced(false),
    speedReducedStartTime(0),
    totalSpeedReducedTime(0),
    isRunning(false),
    runStartTime(0),
    totalRunTime(0)
{
    ui->setupUi(this);

    motorPlot = new Plot(this, "Robot speed", "Time", "Speed");
    motorPlot->setSeriesName("Motor Left");
    motorPlot->addSeries("Motor Right");
    motorPlot->addSeries("isSpeedReduced");
    QPen dashedPen(Qt::DashLine);
    dashedPen.setColor(Qt::red);
    QVBoxLayout *tab1Layout = new QVBoxLayout(ui->tabChart1);
    tab1Layout->addWidget(motorPlot);
    ui->tabChart1->setLayout(tab1Layout);

    sensorPlot = new Plot(this, "Sensor error", "Time", "Error");
    QVBoxLayout *tab2Layout = new QVBoxLayout(ui->tabChart2);
    tab2Layout->addWidget(sensorPlot);
    ui->tabChart2->setLayout(tab2Layout);

    plotStartTime = 0;

    motorPlot->setAxisRange(0, 0, -1, 3);

    connect(bluetoothHandler, &BluetoothHandler::deviceFound, this, &MainWindow::captureDeviceProperties);
    connect(bluetoothHandler, &BluetoothHandler::discoveryFinished, this, &MainWindow::searchingFinished);
    connect(bluetoothHandler, &BluetoothHandler::connectionEstablished, this, &MainWindow::connectionEstablished);
    connect(bluetoothHandler, &BluetoothHandler::connectionLost, this, &MainWindow::connectionLost);
    connect(bluetoothHandler, &BluetoothHandler::dataReceived, this, &MainWindow::handleDataReceived);
    connect(bluetoothHandler, &BluetoothHandler::errorOccurred, this, [this](const QString &error)
            { addToLogs(error, false); });

    connect(bootloader, &Bootloader::errorOccurred, this, [this](const QString &error)
            {
                addToLogs(error, false);
                QMessageBox::warning(this, tr("Bootloader Error"), error);
            });
    connect(bootloader, &Bootloader::progressUpdated, ui->progressBarBootloader, &QProgressBar::setValue);
    connect(bootloader, &Bootloader::errorOccurred, [this](const QString &error)
            {
                addToLogs(error, false);
                QMessageBox::warning(this, tr("Bootloader Error"), error);
            });
}

MainWindow::~MainWindow()
{
    delete ui;
}

void MainWindow::on_pushButtonDisconnect_clicked()
{
    bluetoothHandler->disconnectFromDevice();
}

void MainWindow::on_pushButtonConnect_clicked()
{
    QString selectedDeviceName = ui->comboBoxDevices->currentText();

    if (selectedDeviceName.isEmpty())
    {
        addToLogs("No device selected.", false);
        return;
    }

    QBluetoothDeviceInfo selectedDeviceInfo;
    foreach (const QBluetoothDeviceInfo &device, bluetoothHandler->discoveredDevices())
    {
        if (device.name() == selectedDeviceName)
        {
            selectedDeviceInfo = device;
            break;
        }
    }

    if (selectedDeviceInfo.isValid())
    {
        addToLogs("Device found, connect attempting", true);
        bluetoothHandler->connectToDevice(selectedDeviceInfo.address());
    }
    else
    {
        addToLogs("Selected device not found.", false);
    }
}

void MainWindow::on_pushButtonSearch_clicked()
{
    bluetoothHandler->startDeviceDiscovery();
    ui->comboBoxDevices->clear();
    ui->pushButtonSearch->setEnabled(false);
    addToLogs("Bluetooth searching started", true);
}

void MainWindow::captureDeviceProperties(const QBluetoothDeviceInfo &device)
{
    ui->comboBoxDevices->addItem(device.name());
    addToLogs("Device found: " + device.name(), true);

    if (autoConnectInProgress)
    {
        if (device.name() == autoConnectDeviceName)
        {
            addToLogs("AutoConnect: Target device found: " + device.name(), true);

            bluetoothHandler->connectToDevice(device.address());

            autoConnectInProgress = false;
            ui->pushButtonAutoConnect->setEnabled(true);
        }
    }
}

void MainWindow::searchingFinished()
{
    ui->pushButtonSearch->setEnabled(true);
    addToLogs("Searching finished", true);
}

void MainWindow::connectionEstablished()
{
    ui->indicatorConnStatus->setOn(true);
    bluetoothHandler->stopDeviceDiscovery();
    addToLogs("Connection established successfully.", false);
}

void MainWindow::connectionLost()
{
    ui->indicatorConnStatus->setOn(false);
    addToLogs("Connection lost.", false);
}

void MainWindow::handleDataReceived(Command command, const QByteArray &data)
{
    switch (command)
    {
    case Command::ReadNvmData:
    {
        updateNvmLayout(data);
        break;
    }
    case Command::DebugData:
    {
        updateDebugData(data);
        break;
    }
    case Command::BootStartDownload:
    {
        addToLogs("Bootloader Mode enabled.", true);
        break;
    }
    case Command::BootGetVersion:
    {
        QString version = QString::fromLatin1(data);
        addToLogs("Bootloader version received: " + version, false);
        break;
    }
    case Command::BootEraseApp:
    {
        addToLogs("Application erase completed.", true);
        break;
    }
    case Command::BootValidateApp:
    {
        addToLogs("Application validation completed.", true);
        break;
    }
    case Command::GetActiveSession:
    {
        QString session = QString::fromLatin1(data);
        addToLogs("Active session: " + session, false);
        break;
    }
    default:
        break;
    }
}

void MainWindow::on_pushButtonAutoConnect_clicked()
{
    addToLogs("AutoConnect started", true);

    autoConnectDeviceName = "=Linefollower";
    autoConnectInProgress = true;
    bluetoothHandler->startDeviceDiscovery();
    ui->pushButtonAutoConnect->setEnabled(false);
}

void MainWindow::on_pushButtonStart_clicked()
{
    QByteArray data;
    data.append(static_cast<char>(CommandSetMode::Start));
    bluetoothHandler->sendCommand(Command::SetMode, data);
    addToLogs("Start command sent", true);

    totalSpeedReducedTime = 0;
    wasSpeedReduced = false;
    speedReducedStartTime = 0;
    ui->lineEditReducedSpeedTime->setText("0.00");

    isRunning = true;
    runStartTime = QDateTime::currentMSecsSinceEpoch();
    totalRunTime = 0;
    ui->lineEditTurnOnTime->setText("0.00");
}

void MainWindow::on_pushButtonStop_clicked()
{
    QByteArray data;
    data.append(static_cast<char>(CommandSetMode::Stop));
    bluetoothHandler->sendCommand(Command::SetMode, data);
    addToLogs("Stop command sent", true);

    if (isRunning)
    {
        qint64 currentTime = QDateTime::currentMSecsSinceEpoch();
        totalRunTime += currentTime - runStartTime;
        isRunning = false;
    }

    if (wasSpeedReduced)
    {
        qint64 currentTime = QDateTime::currentMSecsSinceEpoch() - plotStartTime;
        totalSpeedReducedTime += currentTime - speedReducedStartTime;
        wasSpeedReduced = false;
    }
}

void MainWindow::on_pushButtonReset_clicked()
{
    bluetoothHandler->sendCommand(Command::Reset, nullptr);
    addToLogs("Reset command sent", true);
}

void MainWindow::on_pushButtonCalibrate_clicked()
{
    bluetoothHandler->sendCommand(Command::Calibrate, nullptr);
    addToLogs("Calibrate command sent", true);
}

void MainWindow::on_radioButtonDebugMode_clicked(bool checked)
{
    QByteArray data;

    if (checked)
    {
        plotStartTime = QDateTime::currentMSecsSinceEpoch();
        motorPlot->clear();
        sensorPlot->clear();
        data.append(static_cast<char>(true));
        addToLogs("Debug mode enabled", true);
    }
    else
    {
        data.append(static_cast<char>(false));
        addToLogs("Debug mode disabled", true);
    }

    bluetoothHandler->sendCommand(Command::SetDebugMode, data);
}

void MainWindow::on_pushButtonReadNvm_clicked()
{
    bluetoothHandler->sendCommand(Command::ReadNvmData, nullptr);
    addToLogs("Read NvM command sent", true);
}

void MainWindow::on_pushButtonWriteNvm_clicked()
{
    NVMLayout nvmLayout;

    QLineEdit *const sensorWeights[NVMLayout::SENSORS_NUMBER] = {
        ui->lineEditSensorWeight1, ui->lineEditSensorWeight2, ui->lineEditSensorWeight3,
        ui->lineEditSensorWeight4, ui->lineEditSensorWeight5, ui->lineEditSensorWeight6,
        ui->lineEditSensorWeight7, ui->lineEditSensorWeight8, ui->lineEditSensorWeight9,
        ui->lineEditSensorWeight10, ui->lineEditSensorWeight11, ui->lineEditSensorWeight12};
    QLineEdit *const sensorThresholds[NVMLayout::SENSORS_NUMBER] = {
        ui->lineEditSensorCalib1, ui->lineEditSensorCalib2, ui->lineEditSensorCalib3,
        ui->lineEditSensorCalib4, ui->lineEditSensorCalib5, ui->lineEditSensorCalib6,
        ui->lineEditSensorCalib7, ui->lineEditSensorCalib8, ui->lineEditSensorCalib9,
        ui->lineEditSensorCalib10, ui->lineEditSensorCalib11, ui->lineEditSensorCalib12};

    for (int i = 0; i < NVMLayout::SENSORS_NUMBER; ++i)
    {
        nvmLayout.sensors.weights[i] = sensorWeights[i]->text().toInt();
        nvmLayout.sensors.thresholds[i] = sensorThresholds[i]->text().toInt();
    }

    nvmLayout.sensors.errorThreshold = ui->lineEditErrorThreshold->text().toFloat();
    nvmLayout.sensors.fallbackErrorPositive = ui->lineEditfallbackPositive->text().toFloat();
    nvmLayout.sensors.fallbackErrorNegative = ui->lineEditfallbackNegative->text().toFloat();
    nvmLayout.targetSpeed = ui->lineEditTargetSpeed->text().toFloat();
    nvmLayout.timerTimeout[static_cast<size_t>(NVMLayout::LF_Timers::LF_TIMER_NO_LINE_DETECTED)] = ui->lineEditNoLineDetectedTimeout->text().toFloat();
    nvmLayout.timerTimeout[static_cast<size_t>(NVMLayout::LF_Timers::LF_TIMER_REDUCED_SPEED)] = ui->lineEditAngleReducedSpeed->text().toFloat();
    nvmLayout.timerTimeout[static_cast<size_t>(NVMLayout::LF_Timers::LF_TIMER_SENSORS_STABILIZE)] = ui->lineEditSensorsStabilizeTime->text().toFloat();
    nvmLayout.timerTimeout[static_cast<size_t>(NVMLayout::LF_Timers::LF_TIMER_CALIBRATION)] = ui->lineEditCalibrationTime->text().toFloat();

    struct PidSettingsUI
    {
        PIDSettings &pid;
        QLineEdit *lineEditKp;
        QLineEdit *lineEditKi;
        QLineEdit *lineEditKd;
        QLineEdit *lineEditIntMax;
        QLineEdit *lineEditIntMin;
        QLineEdit *lineEditOutputMax;
        QLineEdit *lineEditOutputMin;
    };

    PidSettingsUI pidSettingsUI[] = {
        {nvmLayout.pidStgSensor, ui->lineEditPid1Kp, ui->lineEditPid1Ki, ui->lineEditPid1Kd,
         ui->lineEditPid1IntMax, ui->lineEditPid1IntMin, ui->lineEditPid1OutputMax, ui->lineEditPid1OutputMin},
        {nvmLayout.pidStgEncoderLeft, ui->lineEditPid2Kp, ui->lineEditPid2Ki, ui->lineEditPid2Kd,
         ui->lineEditPid2IntMax, ui->lineEditPid2IntMin, ui->lineEditPid2OutputMax, ui->lineEditPid2OutputMin},
        {nvmLayout.pidStgEncoderRight, ui->lineEditPid3Kp, ui->lineEditPid3Ki, ui->lineEditPid3Kd,
         ui->lineEditPid3IntMax, ui->lineEditPid3IntMin, ui->lineEditPid3OutputMax, ui->lineEditPid3OutputMin}};

    for (const PidSettingsUI &settings : pidSettingsUI)
    {
        settings.pid.kp = settings.lineEditKp->text().toFloat();
        settings.pid.ki = settings.lineEditKi->text().toFloat();
        settings.pid.kd = settings.lineEditKd->text().toFloat();
        settings.pid.integralMax = settings.lineEditIntMax->text().toFloat();
        settings.pid.integralMin = settings.lineEditIntMin->text().toFloat();
        settings.pid.outputMax = settings.lineEditOutputMax->text().toFloat();
        settings.pid.outputMin = settings.lineEditOutputMin->text().toFloat();
    }

    QByteArray data(nvmLayout.size(), Qt::Uninitialized);
    nvmLayout.serializeToArray(reinterpret_cast<uint8_t *>(data.data()));

    bluetoothHandler->sendCommand(Command::WriteNvmData, data);

    addToLogs("Write NvM command sent", true);
}

void MainWindow::updateNvmLayout(const QByteArray &data)
{
    NVMLayout nvmLayout;

    nvmLayout.parseFromArray(reinterpret_cast<const uint8_t *>(data.data()));

    QLineEdit *const sensorWeights[NVMLayout::SENSORS_NUMBER] = {
        ui->lineEditSensorWeight1, ui->lineEditSensorWeight2, ui->lineEditSensorWeight3,
        ui->lineEditSensorWeight4, ui->lineEditSensorWeight5, ui->lineEditSensorWeight6,
        ui->lineEditSensorWeight7, ui->lineEditSensorWeight8, ui->lineEditSensorWeight9,
        ui->lineEditSensorWeight10, ui->lineEditSensorWeight11, ui->lineEditSensorWeight12};
    QLineEdit *const sensorThresholds[NVMLayout::SENSORS_NUMBER] = {
        ui->lineEditSensorCalib1, ui->lineEditSensorCalib2, ui->lineEditSensorCalib3,
        ui->lineEditSensorCalib4, ui->lineEditSensorCalib5, ui->lineEditSensorCalib6,
        ui->lineEditSensorCalib7, ui->lineEditSensorCalib8, ui->lineEditSensorCalib9,
        ui->lineEditSensorCalib10, ui->lineEditSensorCalib11, ui->lineEditSensorCalib12};

    for (int i = 0; i < NVMLayout::SENSORS_NUMBER; ++i)
    {
        sensorWeights[i]->setText(QString::number(nvmLayout.sensors.weights[i]));
        sensorThresholds[i]->setText(QString::number(nvmLayout.sensors.thresholds[i]));
    }

    ui->lineEditErrorThreshold->setText(QString::number(nvmLayout.sensors.errorThreshold));
    ui->lineEditfallbackPositive->setText(QString::number(nvmLayout.sensors.fallbackErrorPositive));
    ui->lineEditfallbackNegative->setText(QString::number(nvmLayout.sensors.fallbackErrorNegative));
    ui->lineEditTargetSpeed->setText(QString::number(nvmLayout.targetSpeed));
    ui->lineEditNoLineDetectedTimeout->setText(QString::number( nvmLayout.timerTimeout[static_cast<size_t>(NVMLayout::LF_Timers::LF_TIMER_NO_LINE_DETECTED)]));
    ui->lineEditAngleReducedSpeed->setText(QString::number( nvmLayout.timerTimeout[static_cast<size_t>(NVMLayout::LF_Timers::LF_TIMER_REDUCED_SPEED)]));
    ui->lineEditSensorsStabilizeTime->setText(QString::number( nvmLayout.timerTimeout[static_cast<size_t>(NVMLayout::LF_Timers::LF_TIMER_SENSORS_STABILIZE)]));
    ui->lineEditCalibrationTime->setText(QString::number( nvmLayout.timerTimeout[static_cast<size_t>(NVMLayout::LF_Timers::LF_TIMER_CALIBRATION)]));
    sensorPlot->setAxisRange(0, 0, nvmLayout.sensors.fallbackErrorNegative - 1, nvmLayout.sensors.fallbackErrorPositive + 1);

    struct PidSettings
    {
        const PIDSettings &pid;
        QLineEdit *lineEditKp;
        QLineEdit *lineEditKi;
        QLineEdit *lineEditKd;
        QLineEdit *lineEditIntMax;
        QLineEdit *lineEditIntMin;
        QLineEdit *lineEditOutputMax;
        QLineEdit *lineEditOutputMin;
    };

    PidSettings pidSettings[] = {
        {nvmLayout.pidStgSensor, ui->lineEditPid1Kp, ui->lineEditPid1Ki, ui->lineEditPid1Kd,
         ui->lineEditPid1IntMax, ui->lineEditPid1IntMin, ui->lineEditPid1OutputMax, ui->lineEditPid1OutputMin},
        {nvmLayout.pidStgEncoderLeft, ui->lineEditPid2Kp, ui->lineEditPid2Ki, ui->lineEditPid2Kd,
         ui->lineEditPid2IntMax, ui->lineEditPid2IntMin, ui->lineEditPid2OutputMax, ui->lineEditPid2OutputMin},
        {nvmLayout.pidStgEncoderRight, ui->lineEditPid3Kp, ui->lineEditPid3Ki, ui->lineEditPid3Kd,
         ui->lineEditPid3IntMax, ui->lineEditPid3IntMin, ui->lineEditPid3OutputMax, ui->lineEditPid3OutputMin}};

    for (const PidSettings &settings : pidSettings)
    {
        settings.lineEditKp->setText(QString::number(settings.pid.kp));
        settings.lineEditKi->setText(QString::number(settings.pid.ki));
        settings.lineEditKd->setText(QString::number(settings.pid.kd));
        settings.lineEditIntMax->setText(QString::number(settings.pid.integralMax));
        settings.lineEditIntMin->setText(QString::number(settings.pid.integralMin));
        settings.lineEditOutputMax->setText(QString::number(settings.pid.outputMax));
        settings.lineEditOutputMin->setText(QString::number(settings.pid.outputMin));
    }

    addToLogs("NvM layout updated.", true);
}

void MainWindow::updateDebugData(const QByteArray &data)
{
    DebugData debugData;

    debugData.parseFromArray(reinterpret_cast<const uint8_t *>(data.data()));

    QLineEdit *const sensorValues[DebugData::SENSORS_NUMBER] = {
        ui->lineEditSensorValue1, ui->lineEditSensorValue2, ui->lineEditSensorValue3, ui->lineEditSensorValue4, 
        ui->lineEditSensorValue5, ui->lineEditSensorValue6, ui->lineEditSensorValue7, ui->lineEditSensorValue8, 
        ui->lineEditSensorValue9, ui->lineEditSensorValue10, ui->lineEditSensorValue11, ui->lineEditSensorValue12};

    QLedIndicator *const sensorLeds[DebugData::SENSORS_NUMBER] = {
        ui->sensorLed1, ui->sensorLed2, ui->sensorLed3, ui->sensorLed4,
        ui->sensorLed5, ui->sensorLed6, ui->sensorLed7, ui->sensorLed8,
        ui->sensorLed9, ui->sensorLed10, ui->sensorLed11, ui->sensorLed12};

    auto averageVelocity = (debugData.motorLeftVelocity + debugData.motorRightVelocity) / 2.0;

    ui->lineEditCurrentError->setText(QString::number(debugData.sensorError));
    ui->lineEditCurrentSpeed->setText(QString::number(averageVelocity));

    for (int i = 0; i < DebugData::SENSORS_NUMBER; ++i)
    {
        sensorValues[i]->setText(QString::number(debugData.sensorValues[i]));
        sensorLeds[i]->setOn(debugData.sensorValues[i] > 3000);
    }

    qint64 currentTime = QDateTime::currentMSecsSinceEpoch() - plotStartTime;
    sensorPlot->addDataPoint(currentTime, debugData.sensorError);
    motorPlot->addDataPoint(0, currentTime, debugData.motorLeftVelocity);
    motorPlot->addDataPoint(1, currentTime, debugData.motorRightVelocity);
    motorPlot->addDataPoint(2, currentTime, debugData.isSpeedReduced ? 1.0 : 0.0);

    if (debugData.isSpeedReduced)
    {
        if (!wasSpeedReduced)
        {
            speedReducedStartTime = currentTime;
            wasSpeedReduced = true;
        }
    }
    else
    {
        if (wasSpeedReduced)
        {
            totalSpeedReducedTime += currentTime - speedReducedStartTime;
            wasSpeedReduced = false;
        }
    }

    double totalTimeInSeconds = totalSpeedReducedTime / 1000.0;

    if (wasSpeedReduced)
    {
        totalTimeInSeconds += (currentTime - speedReducedStartTime) / 1000.0;
    }
    ui->lineEditReducedSpeedTime->setText(QString::number(totalTimeInSeconds, 'f', 2));

    if (isRunning)
    {
        qint64 elapsedTime = totalRunTime + (currentTime + plotStartTime - runStartTime);
        double elapsedTimeInSeconds = elapsedTime / 1000.0;
        ui->lineEditTurnOnTime->setText(QString::number(elapsedTimeInSeconds, 'f', 2));
    }
    else
    {
        double elapsedTimeInSeconds = totalRunTime / 1000.0;
        ui->lineEditTurnOnTime->setText(QString::number(elapsedTimeInSeconds, 'f', 2));
    }
}

void MainWindow::addToLogs(const QString &msg, bool isDebugMsg)
{
    QString currentTime = QDateTime::currentDateTime().toString("yyyy.MM.dd hh:mm:ss");
    const QString msgLog = currentTime + "   " + msg;

    if (isDebugMsg)
    {
        if (ui->radioButtonDebugLogs->isChecked())
        {
            ui->textEditLogs->append(msgLog);
        }
    }
    else
    {
        ui->textEditLogs->append(msgLog);
    }
}

void MainWindow::on_pushButtonClearLogs_clicked()
{
    ui->textEditLogs->clear();
}

void MainWindow::on_pushButtonSaveLogs_clicked()
{
    QString fileName = QFileDialog::getSaveFileName(this, tr("Save Logs"), "", tr("Text Files (*.txt);;All Files (*)"));

    if (fileName.isEmpty())
    {
        return;
    }

    QFile file(fileName);
    if (!file.open(QIODevice::WriteOnly | QIODevice::Text))
    {
        QMessageBox::warning(this, tr("Unable to open file"), file.errorString());
        return;
    }

    QTextStream out(&file);
    out << ui->textEditLogs->toPlainText();

    file.close();

    QMessageBox::information(this, tr("Logs Saved"), tr("Logs have been saved to %1").arg(fileName));
}

void MainWindow::on_pushButtonBootEnter_clicked()
{
    bootloader->enterBootloader();
}

void MainWindow::on_pushButtonBootReadVersion_clicked()
{
    bootloader->getBootloaderVersion();
}

void MainWindow::on_pushButtonBootSelectFile_clicked()
{
    QString filePath = QFileDialog::getOpenFileName(this, tr("Select Firmware File"), "", tr("IntelHex Files (*.hex);;All Files (*)"));
    if (!filePath.isEmpty())
    {
        if (bootloader->selectFirmwareFile(filePath))
        {
            ui->lineEditBootFile->setText(filePath);
        }
    }
}

void MainWindow::on_pushButtonBootErase_clicked()
{
    bootloader->eraseApplication();
}

void MainWindow::on_pushButtonBootFlash_clicked()
{
    bootloader->flashFirmware();
}

void MainWindow::on_pushButtonBootJumpApp_clicked()
{
    bootloader->jumpToApplication();
}

void MainWindow::on_pushButtonBootGetSession_clicked()
{
    bluetoothHandler->sendCommand(Command::GetActiveSession, nullptr);
    addToLogs("Get session command sent", true);
}

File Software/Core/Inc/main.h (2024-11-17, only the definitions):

#define LED12_Pin GPIO_PIN_13
#define LED12_GPIO_Port GPIOC
#define LED11_Pin GPIO_PIN_14
#define LED11_GPIO_Port GPIOC
#define LED10_Pin GPIO_PIN_15
#define LED10_GPIO_Port GPIOC
#define LED9_Pin GPIO_PIN_0
#define LED9_GPIO_Port GPIOC
#define LED8_Pin GPIO_PIN_1
#define LED8_GPIO_Port GPIOC
#define LED7_Pin GPIO_PIN_2
#define LED7_GPIO_Port GPIOC
#define SENSOR12_Pin GPIO_PIN_3
#define SENSOR12_GPIO_Port GPIOC
#define SENSOR11_Pin GPIO_PIN_0
#define SENSOR11_GPIO_Port GPIOA
#define SENSOR10_Pin GPIO_PIN_1
#define SENSOR10_GPIO_Port GPIOA
#define SENSOR9_Pin GPIO_PIN_2
#define SENSOR9_GPIO_Port GPIOA
#define SENSOR8_Pin GPIO_PIN_3
#define SENSOR8_GPIO_Port GPIOA
#define SENSOR7_Pin GPIO_PIN_4
#define SENSOR7_GPIO_Port GPIOA
#define SENSOR6_Pin GPIO_PIN_5
#define SENSOR6_GPIO_Port GPIOA
#define SENSOR5_Pin GPIO_PIN_6
#define SENSOR5_GPIO_Port GPIOA
#define SENSOR4_Pin GPIO_PIN_7
#define SENSOR4_GPIO_Port GPIOA
#define SENSOR3_Pin GPIO_PIN_4
#define SENSOR3_GPIO_Port GPIOC
#define SENSOR2_Pin GPIO_PIN_0
#define SENSOR2_GPIO_Port GPIOB
#define SENSOR1_Pin GPIO_PIN_1
#define SENSOR1_GPIO_Port GPIOB
#define LED6_Pin GPIO_PIN_2
#define LED6_GPIO_Port GPIOB
#define LED5_Pin GPIO_PIN_10
#define LED5_GPIO_Port GPIOB
#define LED4_Pin GPIO_PIN_11
#define LED4_GPIO_Port GPIOB
#define LED3_Pin GPIO_PIN_12
#define LED3_GPIO_Port GPIOB
#define LED2_Pin GPIO_PIN_13
#define LED2_GPIO_Port GPIOB
#define LED1_Pin GPIO_PIN_15
#define LED1_GPIO_Port GPIOB
#define ENCODER_CH1_Pin GPIO_PIN_6
#define ENCODER_CH1_GPIO_Port GPIOC
#define ENCODER_CH2_Pin GPIO_PIN_7
#define ENCODER_CH2_GPIO_Port GPIOC
#define MOTOR1_BIN_Pin GPIO_PIN_9
#define MOTOR1_BIN_GPIO_Port GPIOA
#define MOTOR1_AIN_Pin GPIO_PIN_10
#define MOTOR1_AIN_GPIO_Port GPIOA
#define MOTOR1_PWM_Pin GPIO_PIN_11
#define MOTOR1_PWM_GPIO_Port GPIOA
#define MOTOR2_BIN_Pin GPIO_PIN_2
#define MOTOR2_BIN_GPIO_Port GPIOD
#define MOTOR2_AIN_Pin GPIO_PIN_3
#define MOTOR2_AIN_GPIO_Port GPIOB
#define MOTOR2_PWM_Pin GPIO_PIN_4
#define MOTOR2_PWM_GPIO_Port GPIOB
#define ENCODER_CH1B6_Pin GPIO_PIN_6
#define ENCODER_CH1B6_GPIO_Port GPIOB
#define ENCODER_CH2B7_Pin GPIO_PIN_7
#define ENCODER_CH2B7_GPIO_Port GPIOB

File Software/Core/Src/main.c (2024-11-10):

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
/* Includes ------------------------------------------------------------------*/
#include "main.h"
#include "adc.h"
#include "crc.h"
#include "dma.h"
#include "i2c.h"
#include "tim.h"
#include "usart.h"
#include "gpio.h"

/* USER CODE BEGIN Includes */
#include "lf_main.h"
/* USER CODE END Includes */


/* USER CODE BEGIN PV */
extern const Sensors_Config_T sensorsConfig;

static NVM_Layout_T NvmBlock;
static uint8_t ScpBuffer[SCP_BUFFER_SIZE];

LineFollower_T LineFollower = {
    .debugModeTimer = &htim6,
    .cycleCountReg = &DWT->CYCCNT,
    .nvmInstance = {
        .defaultData = (const uint8_t *)&NvmDefaultData,
        .size = sizeof(NVM_Layout_T),
        .sector = NVM_SECTOR_USED
    },
    .nvmBlock = &NvmBlock,
    .scpInstance = {
        .buffer = ScpBuffer,
        .size = SCP_BUFFER_SIZE,
        .huart = &huart4,
        .commands = lineFollowerCommands,
        .numCommands = sizeof(lineFollowerCommands) / sizeof(lineFollowerCommands[0]),
        .errorHandler = NULL
    },
    .pidSensorInstance = {
        .settings = &NvmBlock.pidStgSensor
    },
    .pidEncoderLeftInstance = {
      .settings =&NvmBlock.pidStgEncoderLeft
    },
    .pidEncoderRightInstance = {
      .settings =&NvmBlock.pidStgEncoderRight
    },
    .encoderLeft = {
      .settings = &encoderSettings,
      .htim = &htim8
    },
    .encoderRight = {
      .settings = &encoderSettings,
      .htim = &htim4
    },
    .sensorsInstance = {
      .config = &sensorsConfig
    },
    .motorLeft = &LeftMotor,
    .motorRight = &RightMotor
};
/* USER CODE END PV */

void SystemClock_Config(void);
static void MPU_Config(void);
/* USER CODE BEGIN 0 */
void HAL_TIM_PeriodElapsedCallback(TIM_HandleTypeDef *htim)
{
    if (htim == &htim6)
    {
        LF_DebugModeTimerCallback(&LineFollower);
    }
}
/* USER CODE END 0 */

/**
  * @brief  The application entry point.
  * @retval int
  */
int main(void)
{

  /* MPU Configuration--------------------------------------------------------*/
  MPU_Config();

  /* MCU Configuration--------------------------------------------------------*/

  /* Reset of all peripherals, Initializes the Flash interface and the Systick. */
  HAL_Init();

  /* Configure the system clock */
  SystemClock_Config();

  /* Initialize all configured peripherals */
  MX_GPIO_Init();
  MX_DMA_Init();
  MX_ADC1_Init();
  MX_I2C1_Init();
  MX_UART4_Init();
  MX_TIM3_Init();
  MX_TIM4_Init();
  MX_I2C3_Init();
  MX_TIM1_Init();
  MX_TIM8_Init();
  MX_CRC_Init();
  MX_TIM2_Init();
  MX_TIM6_Init();
  /* USER CODE BEGIN 2 */
  LF_Init(&LineFollower);
  __enable_irq();
  /* USER CODE END 2 */

  /* Infinite loop */
  /* USER CODE BEGIN WHILE */
  while (1)
  {
    LF_MainFunction(&LineFollower);
    /* USER CODE END WHILE */

    /* USER CODE BEGIN 3 */
  }
  /* USER CODE END 3 */
}

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
 /* MPU Configuration */

void MPU_Config(void)
{
  MPU_Region_InitTypeDef MPU_InitStruct = {0};

  /* Disables the MPU */
  HAL_MPU_Disable();

  /** Initializes and configures the Region and the memory to be protected
  */
  MPU_InitStruct.Enable = MPU_REGION_ENABLE;
  MPU_InitStruct.Number = MPU_REGION_NUMBER0;
  MPU_InitStruct.BaseAddress = 0x0;
  MPU_InitStruct.Size = MPU_REGION_SIZE_4GB;
  MPU_InitStruct.SubRegionDisable = 0x87;
  MPU_InitStruct.TypeExtField = MPU_TEX_LEVEL0;
  MPU_InitStruct.AccessPermission = MPU_REGION_NO_ACCESS;
  MPU_InitStruct.DisableExec = MPU_INSTRUCTION_ACCESS_DISABLE;
  MPU_InitStruct.IsShareable = MPU_ACCESS_SHAREABLE;
  MPU_InitStruct.IsCacheable = MPU_ACCESS_NOT_CACHEABLE;
  MPU_InitStruct.IsBufferable = MPU_ACCESS_NOT_BUFFERABLE;

  HAL_MPU_ConfigRegion(&MPU_InitStruct);
  /* Enables the MPU */
  HAL_MPU_Enable(MPU_PRIVILEGED_DEFAULT);

}

/**
  * @brief  This function is executed in case of error occurrence.
  * @retval None
  */
void Error_Handler(void)
{
  /* USER CODE BEGIN Error_Handler_Debug */
  /* User can add his own implementation to report the HAL error return state */
  __disable_irq();
  while (1)
  {
  }
  /* USER CODE END Error_Handler_Debug */
}

#ifdef  USE_FULL_ASSERT
/**
  * @brief  Reports the name of the source file and the source line number
  *         where the assert_param error has occurred.
  * @param  file: pointer to the source file name
  * @param  line: assert_param error line source number
  * @retval None
  */
void assert_failed(uint8_t *file, uint32_t line)
{
  /* USER CODE BEGIN 6 */
  /* User can add his own implementation to report the file name and line number,
     ex: printf("Wrong parameters value: file %s on line %d\r\n", file, line) */
  /* USER CODE END 6 */
}
#endif /* USE_FULL_ASSERT */

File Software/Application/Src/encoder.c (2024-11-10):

/******************************************************************************************
 *                                        INCLUDES                                        *
 ******************************************************************************************/
#include "encoder.h"
#include <math.h>

/******************************************************************************************
 *                                         DEFINES                                        *
 ******************************************************************************************/
#define PI 3.14159265358979323846f

/******************************************************************************************
 *                                        TYPEDEFS                                        *
 ******************************************************************************************/

/******************************************************************************************
 *                                   FUNCTIONS PROTOTYPES                                 *
 ******************************************************************************************/

/******************************************************************************************
 *                                        VARIABLES                                       *
 ******************************************************************************************/

/******************************************************************************************
 *                                        FUNCTIONS                                       *
 ******************************************************************************************/
/**
 * @brief Initializes the encoder instance
 * @param encoder Pointer to the Encoder_Instance_T structure
 * @return 0 on success, -1 on failure
 */
int Encoder_Init(Encoder_Instance_T *const encoder)
{
    if (encoder == NULL || encoder->htim == NULL)
    {
        return -1;
    }

    (void)HAL_TIM_Encoder_Stop(encoder->htim, TIM_CHANNEL_ALL);
    __HAL_TIM_SET_COUNTER(encoder->htim, 0);

    if (HAL_TIM_Encoder_Start(encoder->htim, TIM_CHANNEL_ALL) != HAL_OK)
    {
        return -1;
    }

    encoder->timerMax = __HAL_TIM_GET_AUTORELOAD(encoder->htim);

    encoder->countPrev = 0;
    encoder->deltaCount = 0;
    encoder->velocity = 0.0f;

    return 0;
}

/**
 * @brief Reads the encoder count
 * @param encoder Pointer to the Encoder_Instance_T structure
 * @return The current count value
 */
int32_t Encoder_GetCount(Encoder_Instance_T *const encoder)
{
    if (encoder == NULL)
    {
        return 0;
    }

    int32_t rawCount = (int32_t)__HAL_TIM_GET_COUNTER(encoder->htim);

    return rawCount;
}

/**
 * @brief Resets the encoder count to zero
 * @param encoder Pointer to the Encoder_Instance_T structure
 */
void Encoder_ResetCount(Encoder_Instance_T *const encoder)
{
    if (encoder == NULL)
    {
        return;
    }

    __HAL_TIM_SET_COUNTER(encoder->htim, 0);
    encoder->countPrev = 0;
    encoder->deltaCount = 0;
}
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

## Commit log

2024-08-31 STM32 project added, pinout configured
2024-08-31 Added PCB layouts
    [schemat.kicad_pcb, schemat.kicad_sch, schemat_1.kicad_sch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]
2024-08-31 PID algorithm implemented
2024-09-01 Pid source files moved to Src/Inc directory
2024-09-02 UART with DMA enabled
2024-09-04 SCP Error Handler added
    [scp.c]
2024-09-04 ADC sensor channels configured in DMA mode
2024-09-05 Sensor component created
2024-09-07 Sensor error calculation implemented
    [linefollower.c, linefollower_config.c, sensors.c]
2024-09-08 Motor timer PWM frequency set to 36kHz
2024-09-10 Pololu TB6612FNG motor driver implemented
2024-09-10 Sensor refactored, created only one manager
2024-09-11 ADC timer trigger configured
2024-09-11 ADC conversion end callback added
2024-09-12 Sensors calibration implemented
2024-09-12 Sensor calibration signal implemented
2024-09-13 Fixed motor driver pointer bug
    [lf_calibrate.c, tb6612_motor.c]
2024-09-14 LedInidiactor plugin implemented
2024-09-14 UI design updated, added linefollower control and sensors sections
2024-09-15 Implemented constexpr size function for nvm and pid classes
2024-09-16 Nvm, Pid handling big and little endian
2024-09-16 QT: Added errors emit in bluetooth handler
    [mainwindow.cpp]
2024-09-17 Sensor calibration threshold added into nvm
2024-09-24 PCB sensor layout updated
    [schemat.kicad_pcb, schemat_2.kicad_sch]
2024-09-29 Fixed SCP data length receiving
    [linefollower_commands.c]
2024-09-29 Debug data send triggered using timer (signal every 50ms)
2024-09-29 Missing critical sections added
    [sensors.c]
2024-09-29 nvm, lf_signal, pid function briefs updated
2024-09-29 All compiler warnings fixed
    [linefollower.c]
2024-10-03 Encoder driver implemented
2024-10-13 Fixed inverted led sensors configuration
    [linefollower_config.c]
2024-10-13 QT: Fixed led indicator update bug
2024-10-13 Nvm write added after sensor calibration
2024-10-13 Added leds effect in bootloader
2024-10-16 Encoder integration with the main algorithm
2024-10-16 Added motor speeds to the debug data
2024-10-21 Minor fixes related to configuration, sensor error calculation
    [main.c, sensors.c]
2024-10-26 Added timeout if no sensor detected line
2024-10-26 Motors velocity result in meters per second
2024-10-27 Fixed bug with reversed motor rotation, updated default nvm values
    [linefollower.c, linefollower_config.c, tb6612_motor.c]
2024-10-30 Sensors module refactored
2024-11-03 Encoder PID adjustment, Changed ADC measurements period from 20ms to 5ms
2024-11-08 Straight line and stabilize detection implemented
    [linefollower_config.c, sensors.c]
2024-11-10 Added timers mechanisms, implemented speed reduction when right angle is detected
2024-11-10 Calibration method uses the timers mechanism
2024-11-10 QT: Added speed reduced to the motor chart, debug information improvements
2024-11-14 Minor fixes in schematics, added gerbers and schematics pdfs
    [schemat.kicad_pcb, schemat.kicad_sch, schemat_1.kicad_sch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]
2024-11-17 Readme images added: Flash memory layout, PCB layouts

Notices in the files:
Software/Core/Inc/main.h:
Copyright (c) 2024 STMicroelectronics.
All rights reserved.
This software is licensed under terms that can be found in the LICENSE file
